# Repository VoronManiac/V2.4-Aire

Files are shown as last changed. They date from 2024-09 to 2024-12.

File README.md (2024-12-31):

# V2.4-Aire #
Each Aire filter has a HEPA particle prefilter followed by an activated charcoal filter and is targeted at Voron 2.4 250/300/350 printers. Ideally, a pair of filters is mounted on either side of the print bed. The design is optimized for high air flow to increase the turnover rate and minimize particulate concentration. <br>

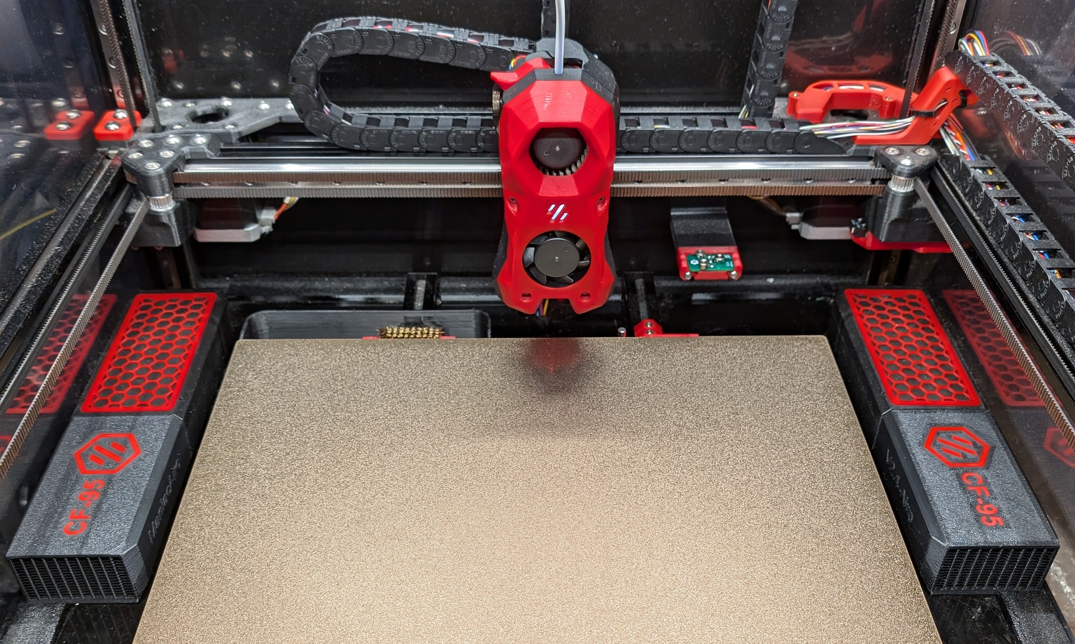
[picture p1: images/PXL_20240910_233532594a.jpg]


Aire uses inexpensive Eufy RoboVAC HEPA filters.  The Eufy HEPA filter sits above the 5015 blower, but sufficient space is provided between the two to prevent the blower from stalling.  The blower exhaust feeds the single piece activated carbon cartridge which attaches to the HEPA/blower section with magnets. Once loaded with charcoal, two small doors slide into place to close off the cartridge. 

As shown below, the air path in the cartridge splits into two sections, passing through a 17mm wide layer of charcoal,  and then gets collected in the output plenums.  The split path and relatively thin width of charcoal reduces blower back pressure and helps increase airflow.  Each 95mm cartridge has similar charcoal capacity compared to NeverMore DuoV5.  If additional capacity is needed, the 95mm cartridge could be redesigned to further increase the charcoal volume by lengthening it, which incidentally would *decrease* the blower back pressure even further and increase airflow.

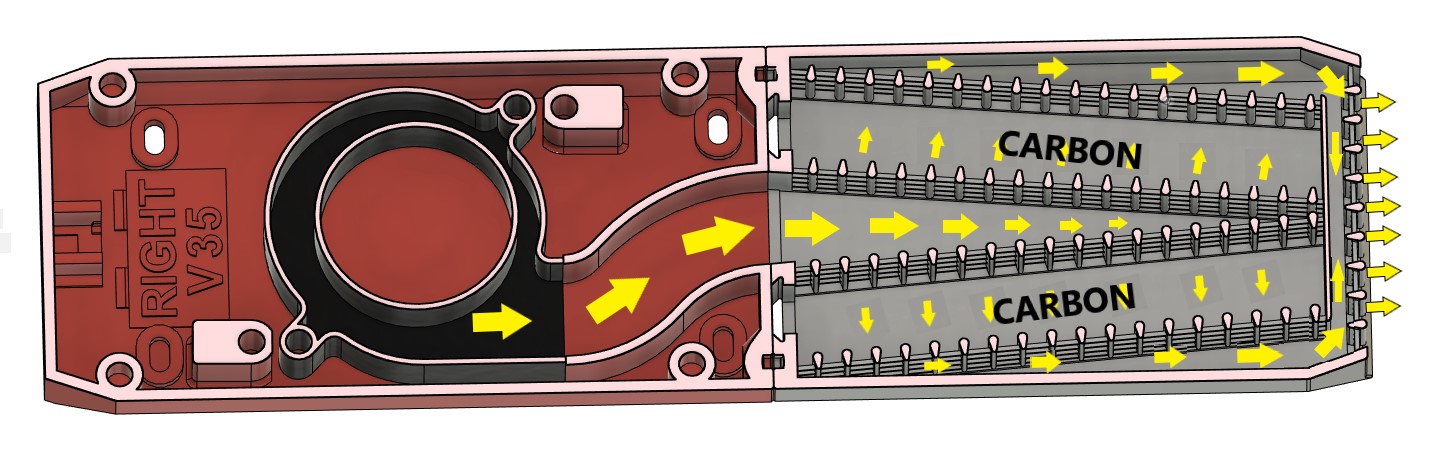
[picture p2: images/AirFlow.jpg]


It is difficult to say how frequently the HEPA filter and charcoal need to be replaced without some direct particle and VOC measurements, but the pic below shows a dirty filter after 4 months of usage compared to a fresh filter. With the Zyltech ABS filament I have been running, the charcoal should last for many weeks of continuous printing.

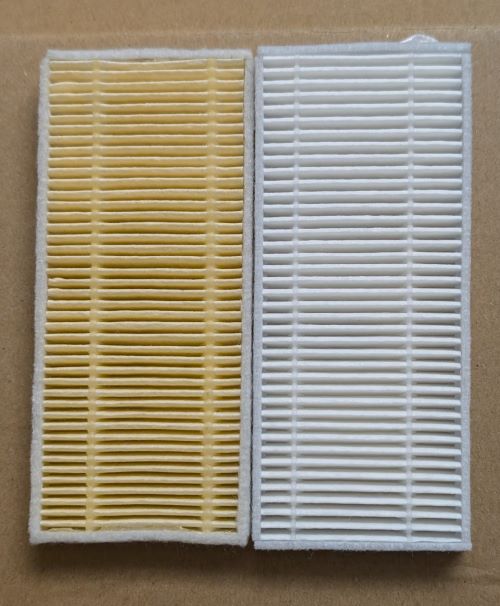
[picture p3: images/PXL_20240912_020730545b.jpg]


## BOM ##
| Qty | Item | Comment |
|:--- |:--- |:----- |
|2 | Eufy RoboVac Filter 110x48x10(mm)| https://www.amazon.com/gp/product/B07F5XK5WN/ref=ppx_yo_dt_b_search_asin_title  |
|2 |GDSTIME 5015 Turbo Dual BB 24V  | https://www.amazon.com/gp/product/B0B1V6JTB8/ref=ppx_yo_dt_b_search_asin_title  |
|2 | 2-Pin 2.5mm JST Male Pin Header | like https://www.digikey.com/en/products/detail/jst-sales-america-inc./B2B-XH-A/1651045  or https://www.amazon.com/gp/product/B08YNFGYNH/ref=ppx_yo_dt_b_search_asin_title|
| 16  | M3x8 BHCS |  |
|4|M3 Half Round T Nuts|https://www.amazon.com/gp/product/B08YNFGYNH/ref=ppx_yo_dt_b_search_asin_title |
| 4 | M3 9mm washer | |
| 12 |  M3xD5.0xL4.0 Heatset Insert | |
| 16 | N52 magnets 6mm dia x 3mm thick| | 
| 2  | 10mm Red/Black 1.5mm Dia heat shrink tubing| |
| bag | activated charcoal | |

## Printing ##

Print in ABS using standard Voron Settings: 40% infill, 4 perimeters, 5 solid bottom/top, no supports.    

A z-lift of 0.1mm seemed to reduce stringing when printing the CarbonFilter grid, but significantly increases the print time.

The CarbonFilter STL is designed to be split into four sub-objects in the slicer for accent colorization.  I found that Paramount Red ABS was somewhat translucent and darkened when a black back layer was applied over the accent. The STL contains an extra color change back layer to cover the red accent color.  I found the red really popped with a white or silver back layer.

## Assembly ##

Insert six heat set inserts into each of the FilterMainL and FilterMainR parts making sure the inserts are flush or below the plastic.
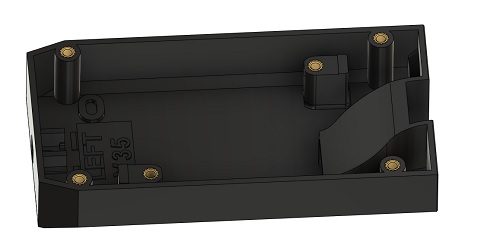
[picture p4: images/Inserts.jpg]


Add M3x8 screws to the four outermost inserts leaving about 3mm of the screw thread exposed.
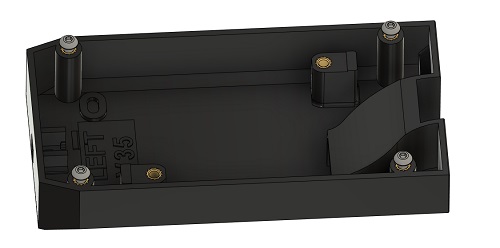
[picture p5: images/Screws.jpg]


Take the perfectly good 5015 blowers and cut the leads to about 80mm.  Solder and heat shrink the blower leads to the 2P JST housings, keeping the red/black orientation matching the original leads.

Insert a soldered JST housing into each of the FilterMain parts, noting the orientation. The gap in the JST connector should face down.  Insert the connector at an angle, then press flat until it snaps into place. 
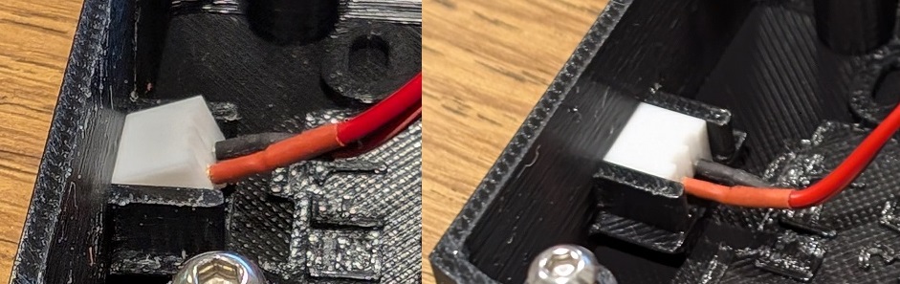
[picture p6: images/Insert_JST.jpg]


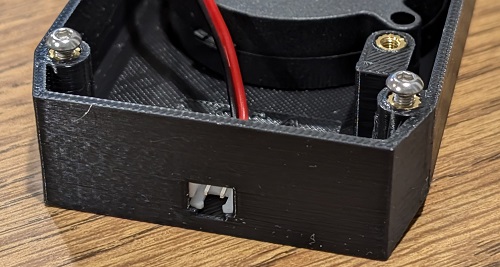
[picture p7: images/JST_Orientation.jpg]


Starting at a slight angle, slide a ConnClamp over each JST housing.  The ConnClamp should snap into place with some modest pressure.
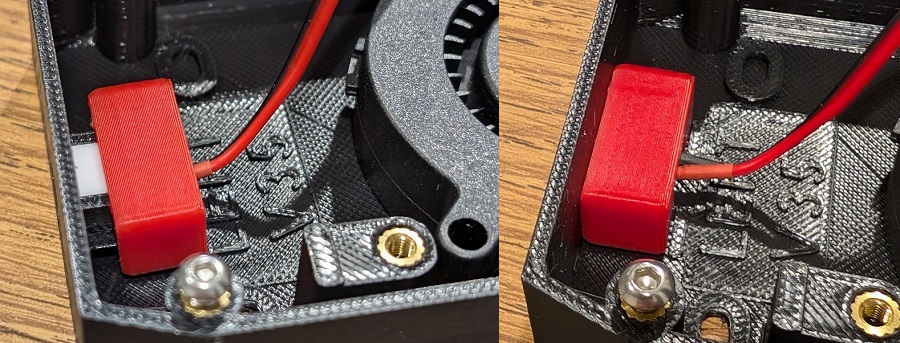
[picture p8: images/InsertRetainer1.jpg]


Orient the 5015 blowers to line up with the exhaust phlenum and secure in place with BlowerHoldDowns and M3x8 screws.  Tuck in the excess blower wire.

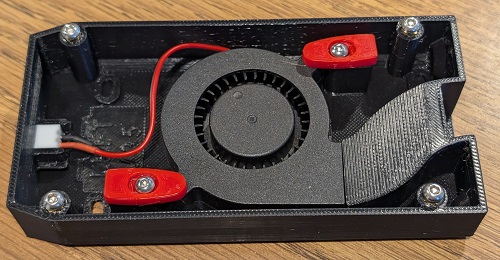
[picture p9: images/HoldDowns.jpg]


Trial fit the FilterTop onto each FilterMain, slide into place and snug up the four retaining screws.  Verify that the FilterTop aligns and squares up with the FilterMain and forms a tight fit with the CarbonFilter cartridge. Depending on your print quality, lightly sand away any 3D print imperfections on the mating surfaces.  It doesn't have to be perfect.  

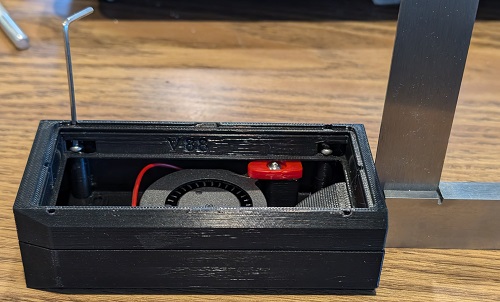
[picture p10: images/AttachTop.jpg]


Inspect the magnet pockets for 3D print irregularities and trial fit the magnets.   A piece of wax paper is a convenient separator between the magnets as they are glued in, allowing the cartridge to be pressed against the FilterMain/FilterTop assembly. Orient the magnet pairs so they attract, separated by the wax paper. When satisified with the fit add a drop of CA to glue the magnets into place.  
  
The RoboVac filter can be inserted with the extraction ribbon facing outwards or inwards.  If facing outwards, it doesn't sit as flat under the foam prefilter and obstructs a small amount of the filter surface.  My preference is to install inwards in which case a small Allen wrench can be inserted as shown to pry out the filter when it comes time for removal.

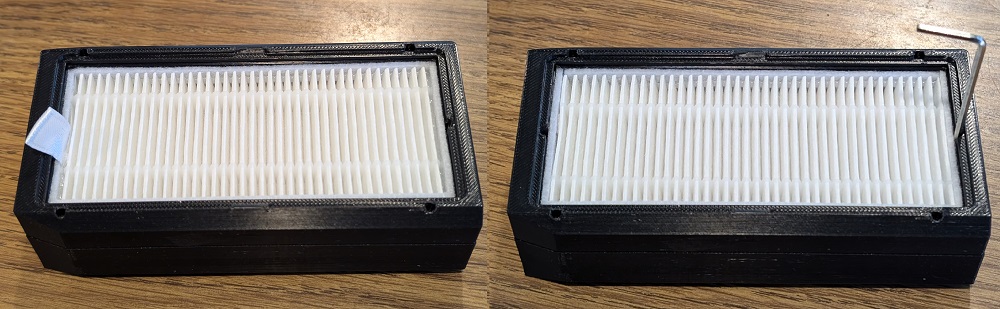
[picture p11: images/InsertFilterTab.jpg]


Add the foam prefilter that comes with with the RoboVac filters and snap the FilterScreen into place.  A  finger nail or small screwdriver can be inserted as shown to pry off the FilterScreen as needed when replacing the filters.

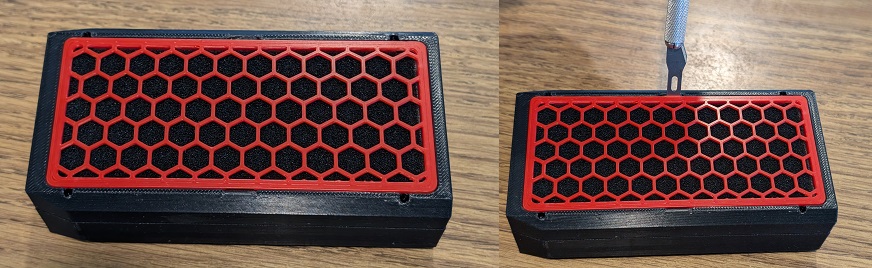
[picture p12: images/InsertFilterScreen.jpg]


I recommend testing each filter before it is installed in the printer. If a power supply is available, check the fan is drawing at least 80mA.  There are a lot of underpowered counterfeit fans in the supply chain that only draw a fraction of this power with drastically reduced airflow.

Check the fit of each FilterDoor by sliding them into the CarbonFilters.  They should just fit and snap into place when fully inserted. Remove any elephant foot or blobs as needed. Note there is a chamfer on the edge of each door that mates into the dovetail grove of the CarbonFilters so be sure to get the orientation correct. Slide the funnel into place as shown and fill each of the two chambers of each CarbonFilter with activated charcoal. Gently tap and jiggle the filter so the carbon settles.  If the chamber is not completely full, air will bypass over the top of the charcoal layer reducing the effectiveness of filter.  Insert the FilterDoor as each chamber is filled.

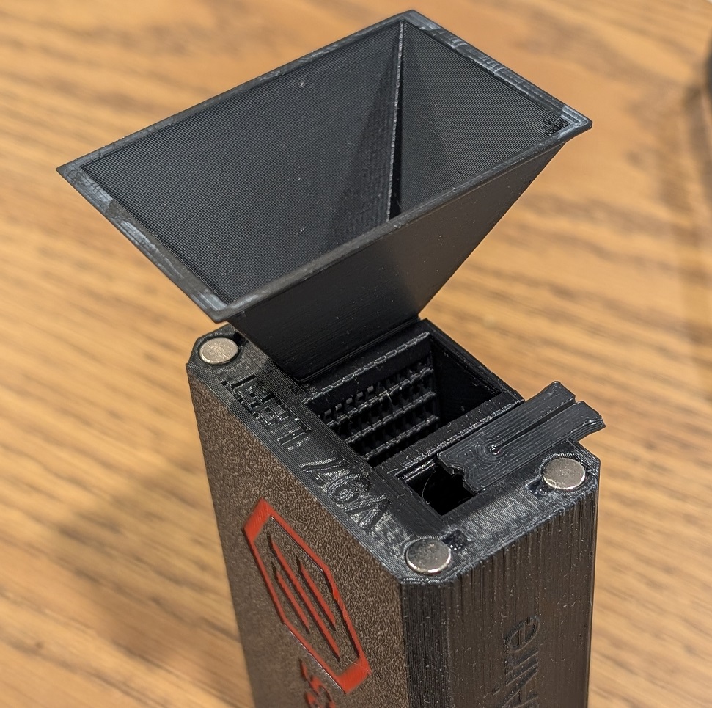
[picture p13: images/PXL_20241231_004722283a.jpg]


## Installation ##

The filters can be mounted so the exhaust is directed towards the front or back of the chamber according to personal preference.  I haven't seen any draft/warping issues with rear mounted filters with front facing exhausts as pictured.

Start by removing the HEPA filters, FilterScreens and the FilterTop of each filter by backing out the four M3 screws holding the FilterTop by a couple of turns.  Removing the FilterTop provides access to the two mounting holes.  Insert two half round T nuts into the 2020 channel and slide so the holes line up with holes in each FilterMain.  The Right and Left FilterMain have unused mounting holes blocked off. Insert the M3x8 screws with M3x9mm washers and secure the FilterMain where indicated below with the yellow arrows.  The [TPU Z belt covers](https://github.com/VoronManiac/Maniac-Chamber-Lighting/blob/main/STL/Common/DeckCornerRightRear.stl) shown are used in the  [Low Glare LED Maniac-Chamber-Lighting](https://github.com/VoronManiac/Maniac-Chamber-Lighting/tree/main) project and have channels for routing the power leads to the filters.  If you decide not to use these z-belt covers, plan out your wire routing for the filter power leads. 

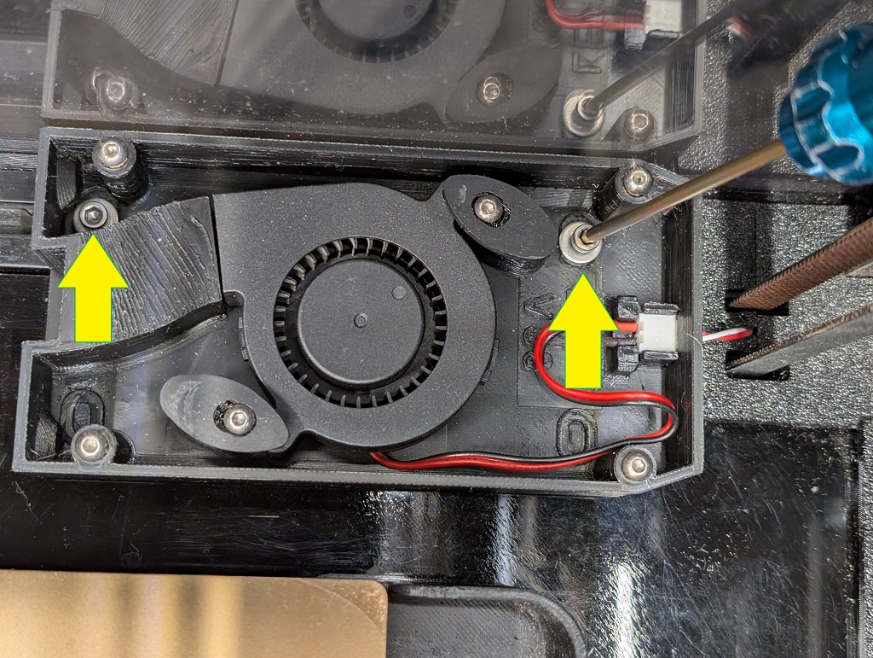
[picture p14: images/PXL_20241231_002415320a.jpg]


Once satisfied with the position tighten the FilterMain into place.    Allow the CarbonFilter cartridge to snap to the FilterMain and FilterTop then lock the FilterTops into place by snugging the four retaining screws with an allen wrench as shown below.  Re-install the HEPA filters, foam prefilter, and FilterScreens.

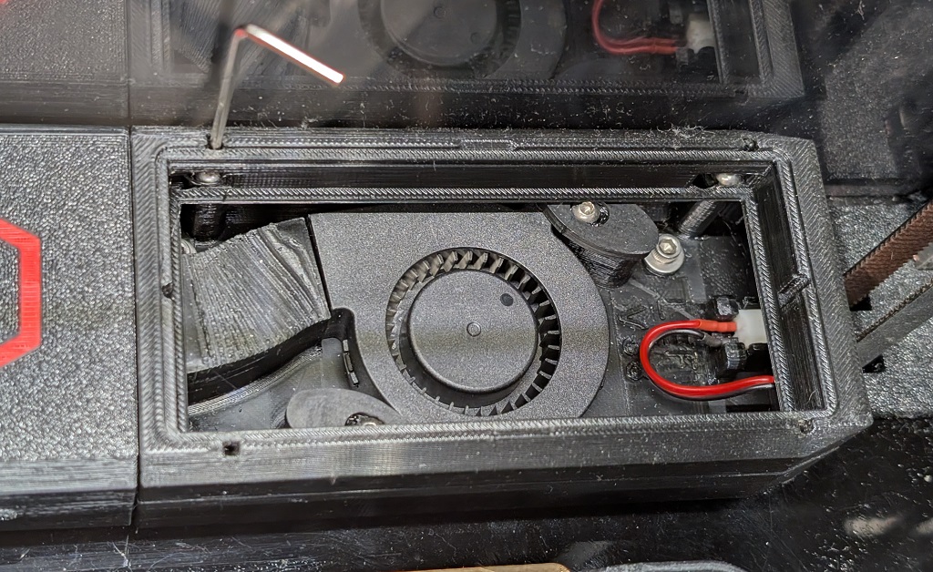
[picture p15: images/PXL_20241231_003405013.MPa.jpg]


Wire routing with power leads connected to JST using the TPU z-belt cover from the LED project as shown below.

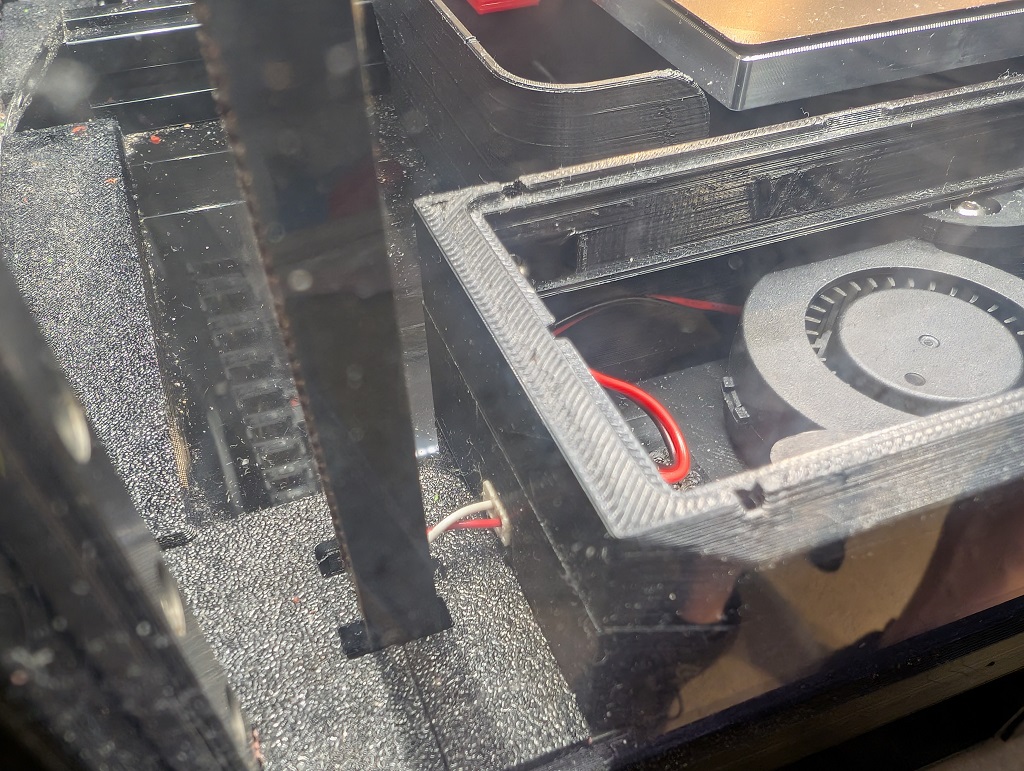
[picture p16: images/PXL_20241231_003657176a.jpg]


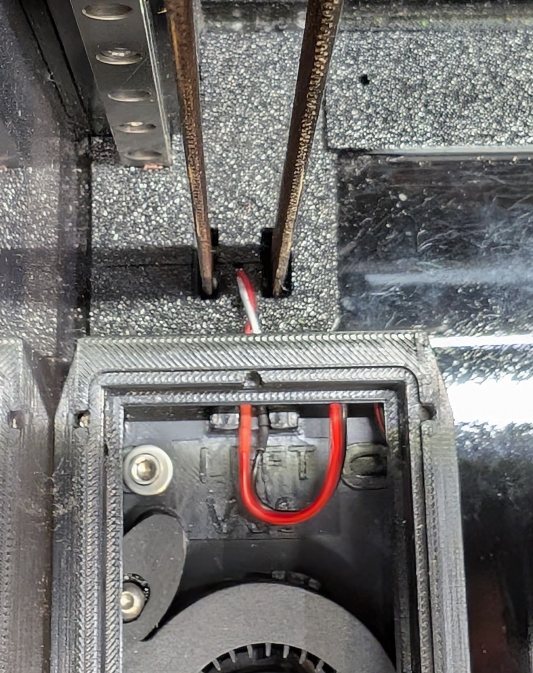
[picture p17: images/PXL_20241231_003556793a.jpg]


## Special Considerations ##
The filter Z height is constrained to 35mm max which is slightly below the print bed surface of a typical V2.4.  Check that your printer has the 35mm of clearance.  In some earlier V2.4 machines, the M3 SHCS that holds the X/Y endstop switch housing in place can be replaced with BHCS or the housing can be modified to completely recess the screws.  The clearance might also be a function of hot end length and z-home switch.<br>

## FW Setup ##
Add the following to `printer.cfg` so that the filters come on when the extruder or bed are above 90C.  The extra airflow across and under the bed helps heat the chamber a bit more quickly at the start of a print.<br>
```
 [heater_fan filter_fan]

  pin: PD12  #machine specific
  kick_start_time: 0.5
  heater: heater_bed, extruder
  heater_temp: 90.0
```

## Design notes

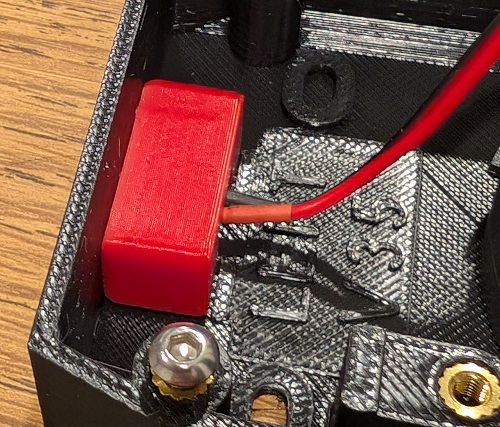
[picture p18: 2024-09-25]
images/SlideRetainer.jpg

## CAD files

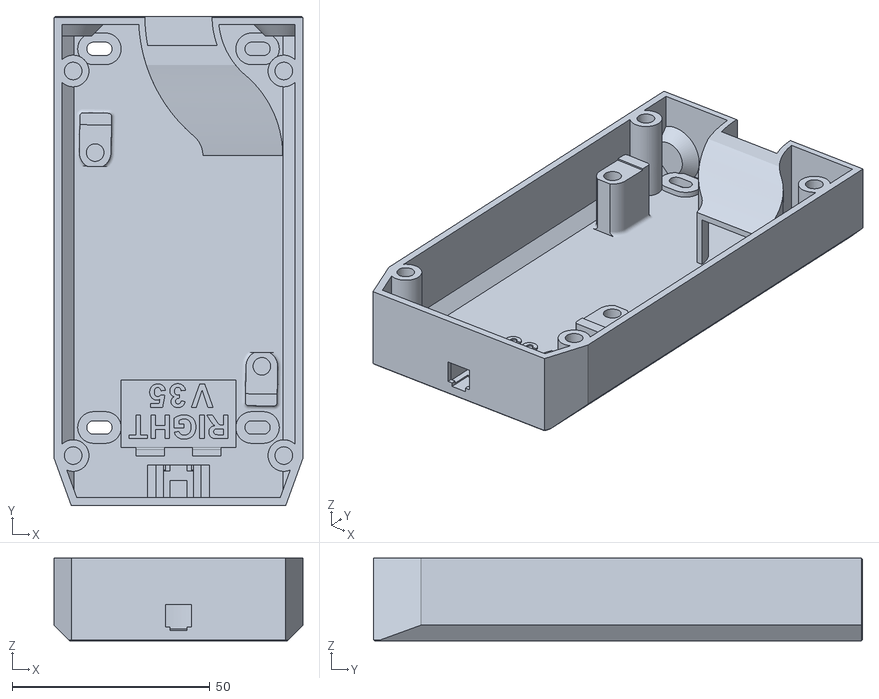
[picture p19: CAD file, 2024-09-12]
STL/FilterMainR_x1_V35.stl
63.0 x 123.8 x 21.0

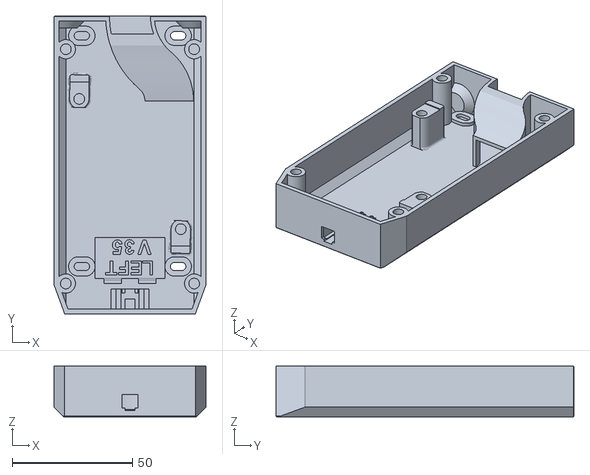
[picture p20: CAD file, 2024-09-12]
STL/FilterMainL_x1_V35.stl
63.0 x 123.8 x 21.0

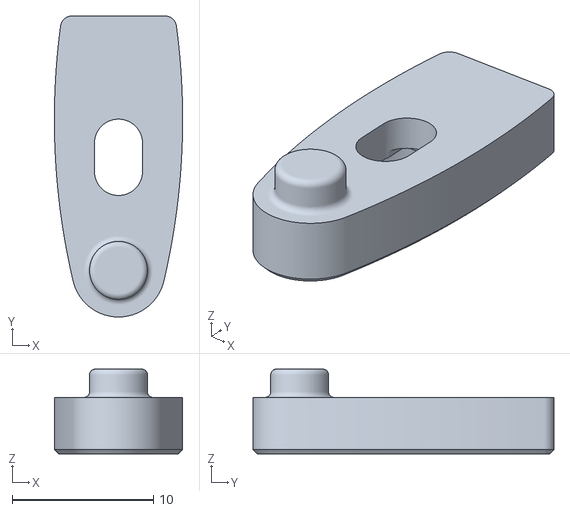
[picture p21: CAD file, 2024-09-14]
STL/BlowerHoldDown_x4_V35.stl
9.08 x 21.3 x 6.00

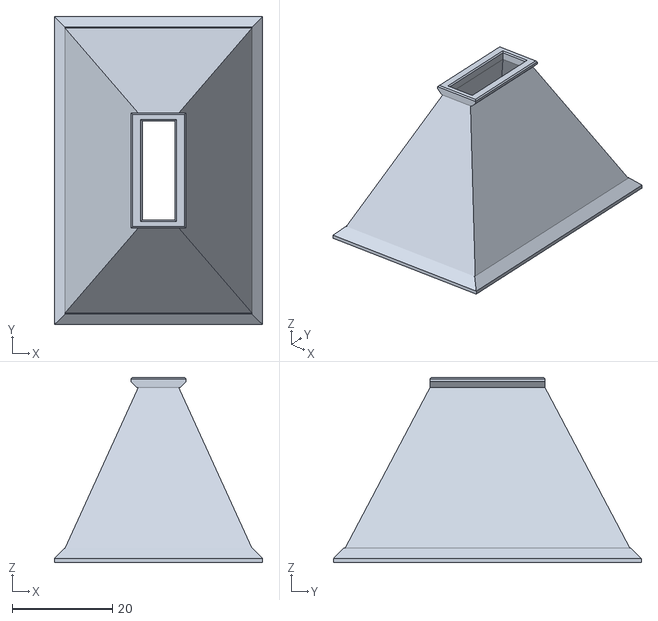
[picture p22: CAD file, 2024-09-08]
STL/FilterFunnel_x1_V35.stl
41.6 x 61.6 x 37.0

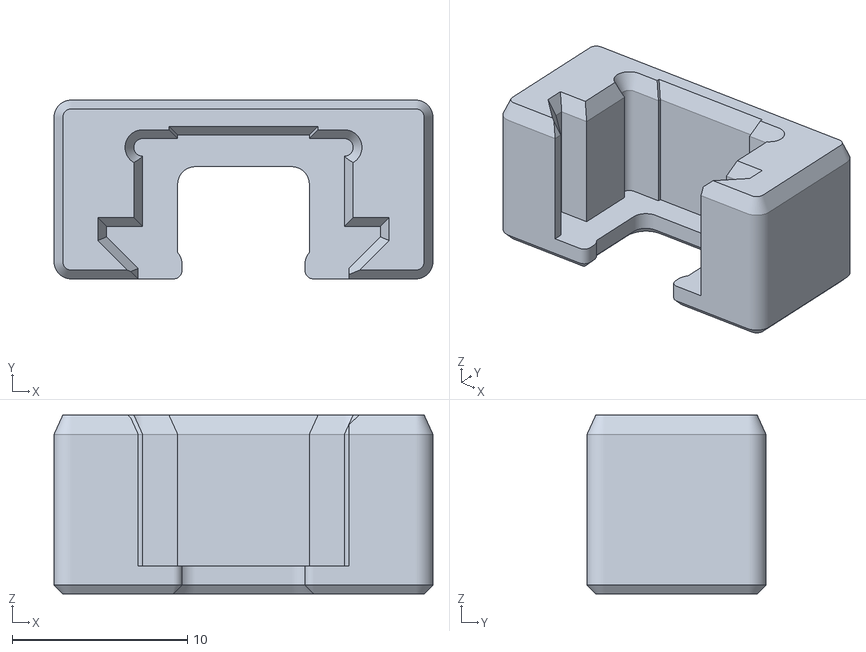
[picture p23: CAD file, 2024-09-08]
STL/ConnClamp_x2_V35.stl
21.6 x 10.2 x 10.2

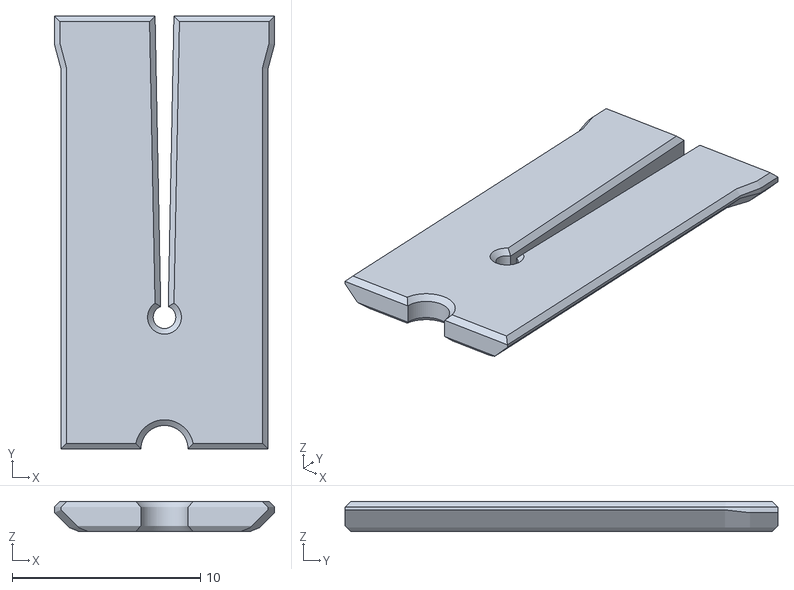
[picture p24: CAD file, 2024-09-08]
STL/FilterDoor_x4_V35.stl
11.7 x 23.0 x 1.60

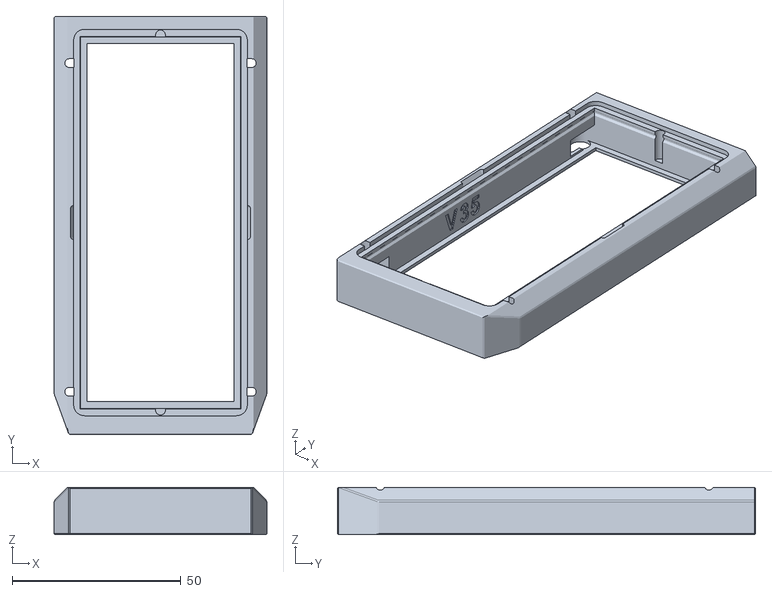
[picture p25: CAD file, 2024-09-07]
STL/FilterTop_x2_V35.stl
63.0 x 123.8 x 14.0

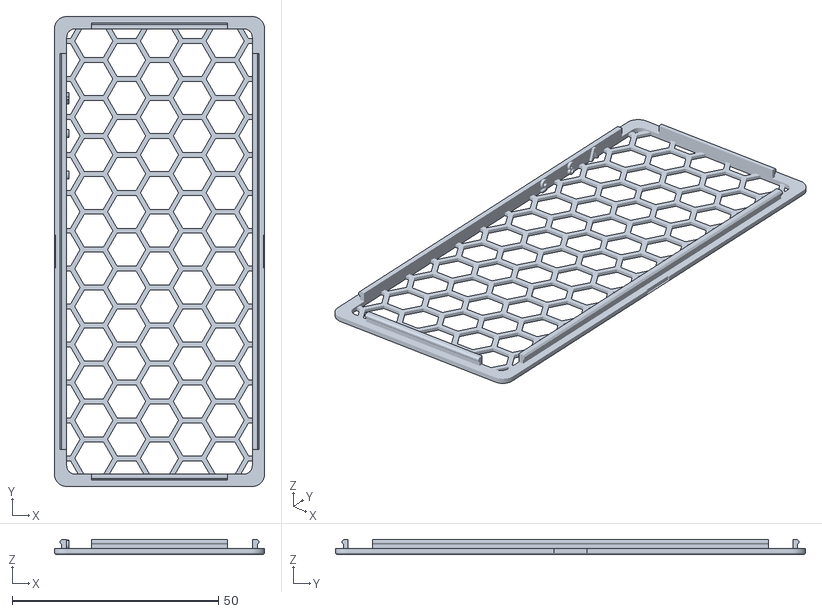
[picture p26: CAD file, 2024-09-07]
STL/(a)_FilterScreen_x2_V35.stl
51.0 x 114.0 x 3.60

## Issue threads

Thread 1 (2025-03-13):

CAD files with Pogo Connectors

NikosSprocket, 2025-03-13:
Hi!
The attached file has the CAD drawings for using Pogo connectors.
Fill free to use as you like.

Thank you for a great design!
Nikos

[V2.4-Aire_V35-Pogo.zip](https://github.com/user-attachments/files/19223016/V2.4-Aire_V35-Pogo.zip)
